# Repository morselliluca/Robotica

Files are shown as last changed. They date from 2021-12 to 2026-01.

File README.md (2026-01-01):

# Robotica

SE NON AVETE VOGLIA DI LEGGERE A FINE README CI SONO LE INFORMAZZIONI PER CONTTATARCI

Tutti i ptogetti robotica del Gruppo DKV Lab<br/>
Siamo un gruppo di 2 persone dell'Itis rossi che hanno partecipato alla Robocup per 4 anni consecutivi con questi progetti.<br/>
il gruppo è formato da:

	Luca Morselli
		-Arduino e Teensyduino:
			-Data collection -> lettura sensori di calore, ultrasuono, riflesso, encoder
			-Serial and comunication -> comunicazione in seriale tra arduino / teensy e Raspberry
			-Movement -> libreria e calibrazione driver e motori dc
		-Pcb design 
		-Mechanical part design
		
	Luca Barban:
		-On Raspberry:
			-Opencv -> riconoscimento caratteri e colori
			-Navigation -> navigazione della mappa
			-Mapping -> creazione della mappa partendo da ultrasuoni o lidar
			-Data Collection -> salvare i dati sulla mappa del nero calore lettere ecc.
			-Serial and comunication -> comunicazione in seriale tra arduino / teensy e Raspberry
			
Cosa troverete all'interno di questa repository:

All'interno di 1. lego line troverete (Line):

	/programmi
		Il codice per la rescue line per un EV3 della lego
		/programmi/Blocchi
			Dei Blocchi custom per leggere il riflesso RGB separatamente da i sensori Stock della lego

All'inerno di 2. project manta troverete (Maze):

	/documentazione
		Un foglio xsl (foglio di calcolo) con tutti i pinout dell'arduino mega, nano e raspberry 
		
	/pcb
		Le Pcb logic e Power usate per il robot + i file gerber per ordinarli
		
	/programma
		/programma/arduino
			/programma/arduino/mega
				il programma per l'arduino mega
			/programma/arduino/nano
				il programma per l'arduino nano
			/programma/arduino/test
				programmi di test vari
		
		/programma/rsby
			programma di test per la raspberry
	
	/scocca
		/scocca/3d
			pezzi da stampare 3d per la scocca (non utilizzati per l'ultima verisone )
		/scocca/logo
			il logo del team
		/scocca/ruote
			ruote da tagliare al laser (non le consiglio, compratele fatte bene Pololu o simili)
		/scocca/taglio
			la scocca del robot da tagliare al laser 
				bello = il piu recente
				manta = delle prove 
				cobra = il primo tentativo
				
	lista.xls 
		la lista dei pezzi che compongono il robot

All'inerno di 3. project Hive troverete (Maze):

	/cagacubi
		le varie versioni del hopper per buttare giu i cubi
		
	/documentazione
		la varia documentazione per tutti i pezzi del robot +  i vari modelli 3d + regole
	
	/foto
		delle foto del robot renderizzato
	
	/pcb 
		file pdf delle schematiche delle 2 pcb del robot + i file gerber per ordinarli
	
	/programma
		/programma/teensy
			il programma per la teensy per interfacciarsi a ros
		/programma/test
			test vari per la teensy e i sensori
	
	/ros documentation
		buona fortuna ragazzi, questo e l'unico pezzo di documentazione ti ros olte il sito ufficiale fatto da cani
	
	/scocca
		disegni di fuzion della scocca del robot per il taglio a laser
	
	/taglio
		progetti in dxf pronti per il taglio laser
		
	Lista.xls
		la lista dei pezzi che compongono il robot

All'inerno di 4. project Help troverete (Line, in aiuto al team A.L.D.O. per i modniali di robotica):

	/La scocca in 3d per la line
	
	/I modelli dai pezzi scelti

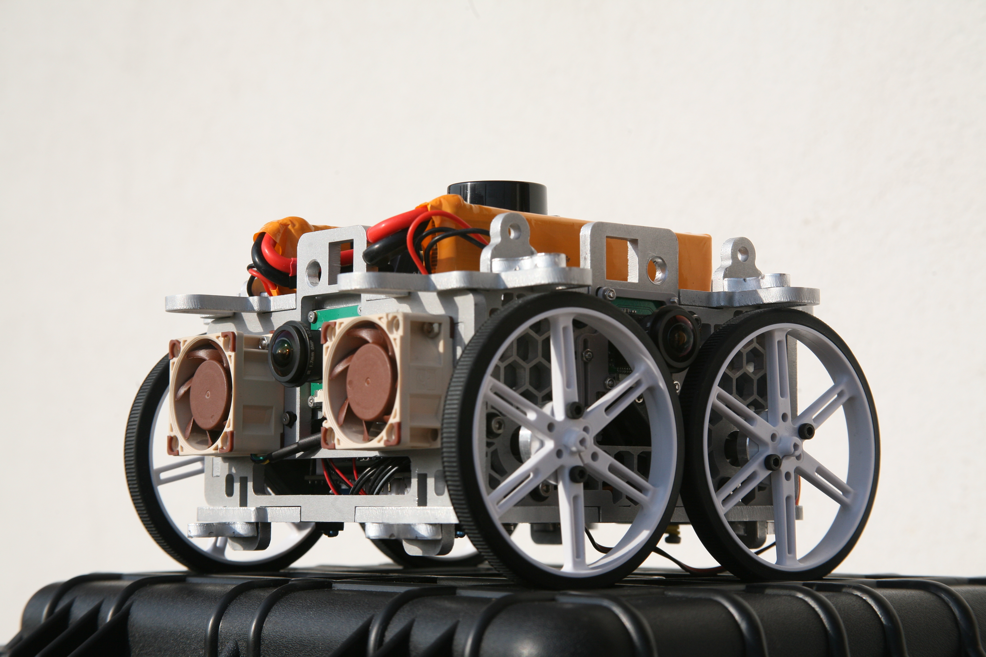
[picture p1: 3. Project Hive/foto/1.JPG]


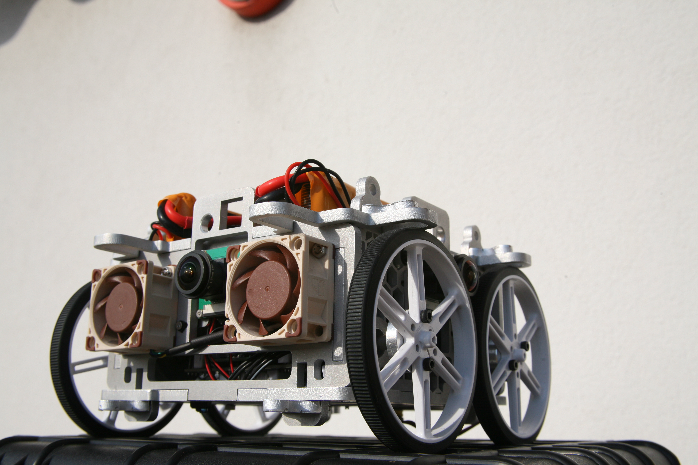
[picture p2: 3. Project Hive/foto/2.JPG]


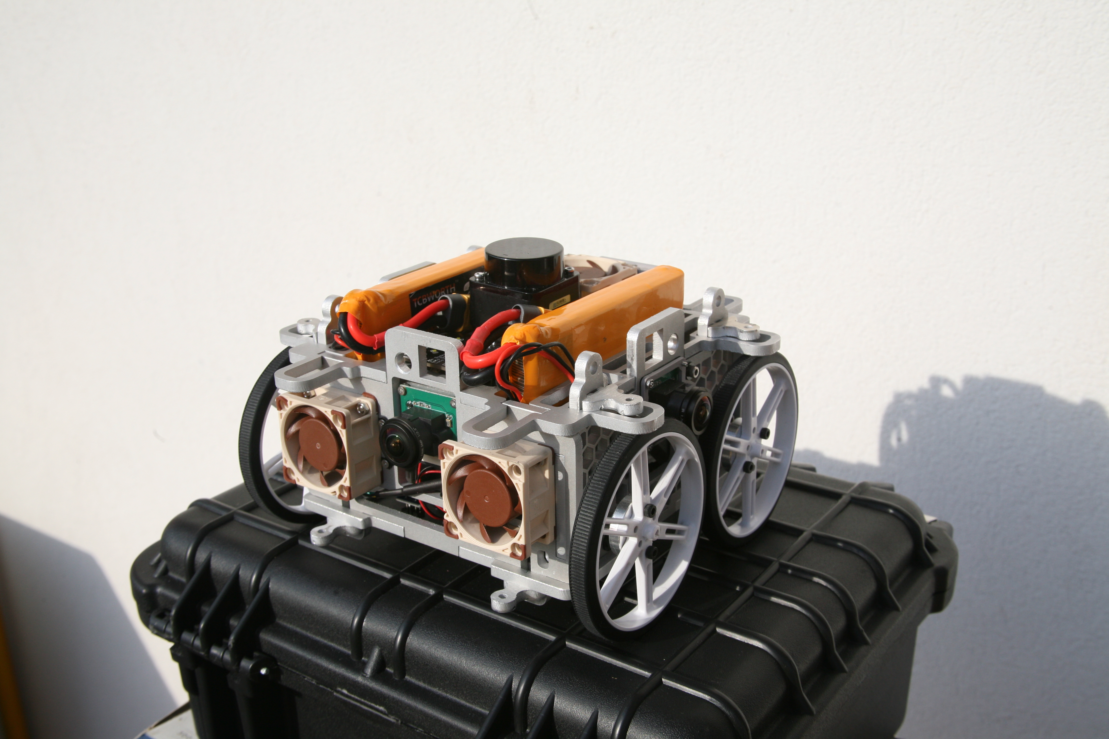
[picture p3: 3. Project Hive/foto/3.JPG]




Faq:

E presente anche una ide di arduino munita di Teensyduino, rosserial e tutte le librerie da noi utilizzate.

Le parti di raspberry degli ultimi 2 progetti mancano e verra aggiunta solo quella dell'ultimo progetto in quanto quella di Manta e stata persa.

I pezzi per il taglio laser sono stati provati principalmente in legno (pippo), plexiglass ed alluminio

I pezzi stampati sono sati stampati solo con stampanti 3d a filamento in quanto della a resina non funzionava (prusa MK.3)

Il grosso dei pezzi e stato acquistato da Aliexpress

Nella lista di Manta ci sono i driver dei motori cinesi NON COMPRATELI si bruciano subito prendete i pololu anche se costano di piu valgono la spesa

Non usate amg8833 come in Manta costano tanto e non e possibile cambiare l'indirizzo i2c nella libreria per leggerli in maniera semplice noi abbiamo usato 2 arduini in piu per questo motvo (i nano), la soluzione migliore e acquistare gli mlx90614

Le batterie consiglio Lipo o 18650 almeno una 3s per portare la tensione intorno i 12v () noi usiamo 2 2s in serie

Consiglio di usare ruote e non cingoli

Consiglio motori con encoder tornano utili per contare i giri che ha fatto la ruota

Per collegare raspberry ad arduino o simili usate la seriale e usate direttamente la porta USB poer evitare di bruciarlo in quanto la maggior parte degli arduino sono a 5v e la raspby supporta solo 3.3v

Quando usate i driver della pololu come MC33926 portate il pin EN -> HIGH e i pin PWM(Negato)/D1 -> Low

I pin INA e INB sono usati per la direzione, vanno messi uno in HIGH uno in LOW 

Da prova_v17 sul progetto Hive le funzioni hanno un timing e vengono eseguite esattamente ogni N millisecondi (la funzione si trova all'interno del void loop)<br/>
	-Odom viene mandata 100HZ<br/>
	-velocita e encoder sono calcolati 1000HZ<br/>

Source:<br/>

Sensori di distanza arduino:<br/>
https://www.youtube.com/watch?v=6F1B_N6LuKw<br/>
https://dronebotworkshop.com/hc-sr04-ultrasonic-distance-sensor-arduino/<br/>

Libreria Pololu vnh5019, la base della libreria custom che troverete in/arduino-1.8.19/libraries/DriverDkv<br/>
https://github.com/pololu/dual-vnh5019-motor-shield<br/>
	
Tutorial per Rosserail + navigation:<br/>
https://www.youtube.com/watch?v=q1u_cC-5Sac<br/>
https://www.youtube.com/watch?v=HLLmV9LQoac<br/>

Ros in generale:<br/>
http://hotblackrobotics.github.io<br/>
https://automaticaddison.com<br/>

Ros navigation:<br/>
https://emanual.robotis.com/docs/en/platform/turtlebot3/learn/#books<br/>
http://wiki.ros.org/ROS/Installation<br/>
http://wiki.ros.org/catkin/Tutorials/create_a_workspace<br/>
http://wiki.ros.org/navigation/Tutorials/RobotSetup<br/>
http://wiki.ros.org/teb_local_planner<br/>
https://answers.ros.org/question/249216/rosserial-posearray-crashes-when-more-than-8-poses-are-used/<br/>

Mlx90614 come usarle e cambiare indirizzo:<br/>
https://www.instructables.com/Multiple-IR-Temperature-Sensors/<br/>
	
Il software per disegnare pcb che consiglio::<br/>
https://easyeda.com/editor<br/>
		
Dove ordinare le pcb online:<br/>
https://jlcpcb.com/<br/>
		
Dove ho ordinato i pezzi tagliati al laser in alluminio:<br/>
https://www.laserboost.com/en/create<br/>
	
Arduino ide (non la 2.0 che non funziona con teensyduino):<br/>
https://www.arduino.cc/en/software<br/>
			
Teensyduino:<br/>
https://www.pjrc.com/teensy/td_usage.html<br/>
https://www.pjrc.com/teensy/teensyduino.html<br/>
https://www.pjrc.com/teensy/td_pulse.html<br/>
https://www.pjrc.com/teensy/td_digital.html<br/>
https://www.pjrc.com/teensy/td_serial.html<br/>
https://www.pjrc.com/teensy/td_uart.html<br/>
		
Software Modellazione 3d (Fusion360 e gratis per gli studenti):<br/>	
https://www.autodesk.com/products/fusion-360/free-trial<br/>

NOTA:<br/>
Usare in maniera informativa nessuno di questi progetti e perfetto ma possono essere usati come una buona base per capire il funzionamento dei vari componenti<br/>
Siamo felici di aiutarvi per qualunque dubbio o perplessita<br/>

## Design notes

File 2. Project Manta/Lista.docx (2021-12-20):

Upgrade

Ci servono

Abbiamo

- 2x amg8833 (telecamere termiche) https://www.melopero.com/shop/sensori/temperatura/melopero-amg8833-grid-eye-ir-array-breakout8833/
- 4x motori(con encoder(non sono uguali a i nostri ma similissimi))

https://www.distrelec.it/it/motore-dc-39-mm-con-cambio-encoder-30-12-vdc-micro-motors-rhe158-30-12v/p/15448402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

- 2x pololu (o simili)

https://www.melopero.com/shop/componenti/pololu-dual-vnh5019-motor-driver-shield-for-arduino/

- 4x telecamere usb

https://www.distrelec.it/it/dash-cam-1280-1024-12-vdc-valueline-svl-carcam10/p/30036026?track=true

- 1x rasperry pi (va bene anche la 3 io ho messo la 4 perche ho trovato questo)

https://www.melopero.com/shop/raspberry-pi-4/raspberry-pi-4-model-b-4gb/

- 1x arduino mega

https://www.melopero.com/shop/arduino-original/arduino-mega-2560-rev3/

- 8x/10x ultrasuoni

https://www.conrad.it/p/sensore-a-ultrasuoni-st1099-iduino-st1099-1616245

- 2x/4x sensori di riflesso
- 2x arduino nano (si puo fare anche senza ma e spararsi nelle palle)

https://www.distrelec.it/it/scheda-nano-arduino-arduino-a000005/p/11096733?track=true

- Legno da 6mm
- 1xRegolatore tesione dc-dc 5v(per raspy)

https://www.melopero.com/shop/componenti/circuiti-integrati/regolatori-circuiti-integrati/pololu-5v-step-upstep-down-voltage-regulator-s7v8f5/

- 1xRegolatore tensione dc-dc 9v(per arduino)

https://www.melopero.com/shop/robotica/pololu-adjustable-step-upstep-down-voltage-regulator-s8v3a/

- 1xRegolatore tensione dc-dc 12v (almeno 4-5A per motori)

https://www.conrad.it/p/scheda-di-sviluppo-buckboost-1875989

- 1xGiroscopio

https://it.rs-online.com/web/p/kit-di-sviluppo-di-sensore/7813033/

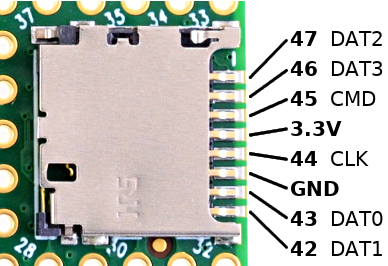
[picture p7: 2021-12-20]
3. Project Hive/Documentazione/Teensy 4.1/Teensy® 4.1_files/teensy41_sdcard_pinout.png

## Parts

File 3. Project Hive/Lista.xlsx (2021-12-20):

Name | Link | Link 3D | -fare o cercare: --oled --batteria -controllare le misure di quelli scaricati -scaricare e uplodare tutti i file sia nella cartella assemblato che nella cartella documentazione (in documentazione ogni pezzo deve avere la sua cartella con il modello 3d e la datasheet se non ce mettilo)
MC33926 | https://www.pololu.com/product/1213
Mlx90614 | https://it.aliexpress.com/item/1005001608889968.html | https://grabcad.com/library/ir-thermo-sensor-hw-691-mlx90614-1
TCRT5000 | https://it.aliexpress.com/item/1899471977.html | https://gallery.autodesk.com/fusion360/projects/135445/sensor-mh-tcrt5000-seguir-trayectoria
LD06 | https://www.inno-maker.com/product/lidar-ld06/
Teensy 4.1 | https://www.sparkfun.com/products/16771
Arducam Multi Camera Adapter Module V2.2 | https://www.uctronics.com/arducam-multi-camera-adapter-module-v2-2-for-raspberry-pi-4-3b-3b-5mp-and-8mp-cameras-compatible-with-arducam-mipi-cameras.html | https://www.uctronics.com/camera-modules/camera-multiplexer/arducam-multi-camera-adapter-module-v2-2-for-raspberry-pi-4-3b-3b-5mp-and-8mp-cameras-compatible-w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
Telecamere | https://it.aliexpress.com/item/1005001597402383.html | https://grabcad.com/library/raspberry-pi-camera-ov5647-1
Ruote | https://www.pololu.com/product/1439 | https://www.pololu.com/product/1439
Adattatori | https://www.pololu.com/product/1083 | https://www.pololu.com/product/1083
Case Rpi | https://it.aliexpress.com/item/1005001691525070.html
Kit jst | https://it.aliexpress.com/item/4000922512405.html
5m cavo awg30 flat 10 fili | https://it.aliexpress.com/item/1841428393.html
Kit jst 8pin | https://it.aliexpress.com/item/1005001628752083.html
ssr | https://it.aliexpress.com/item/32795333121.html
buck converter | https://it.aliexpress.com/item/1005001974967230.html
BNO055 (layout adafruit) | https://it.aliexpress.com/item/1005001641606973.html
condensatore 5v piccolino per raspy | https://it.aliexpress.com/item/32786266119.html
condensatori 12v | https://it.aliexpress.com/item/4000559256747.html
oled arduino i2c quello quadrato non rettangolare | https://it.aliexpress.com/item/1005001908498879.html
Usb c breakout | https://it.aliexpress.com/item/1005001337982060.html
cavi usb micro to usb 90° | https://it.aliexpress.com/item/4000069186507.html
lipo tester | https://it.aliexpress.com/item/4000187507483.html
led Quadrati | https://it.aliexpress.com/item/32954620575.html
Fan 5010 5v | https://it.aliexpress.com/item/32847821588.html | https://gallery.autodesk.com/projects/148644/fan-50x50x10mm?searched=
Raspy | https://www.amazon.com/Raspberry-Model-2019-Quad-Bluetooth/dp/B07TC2BK1X | https://www.thingiverse.com/thing:3778297 |  | Su PCB
Switch | https://www.aliexpress.com/item/32919390284.html | https://gallery.autodesk.com/projects/156746/rocker-toggle-15a-250v-20a-125v-spst-2pin-onoff-switch?searched= |  | Non Servono
Led | https://www.aliexpress.com/item/32874413253.html | https://gallery.autodesk.com/projects/all#query=led&filters=%5B%5D&sort=relevance |  | Fatti da Alin
Batteria |  |  |  | Da Fare
Motore | https://www.banggood.com/Chihai-DC-12V-240rpm-Encoder-Motor-L-Type-Gear-Motor-p-1309847.html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 |  |  | Da Fare

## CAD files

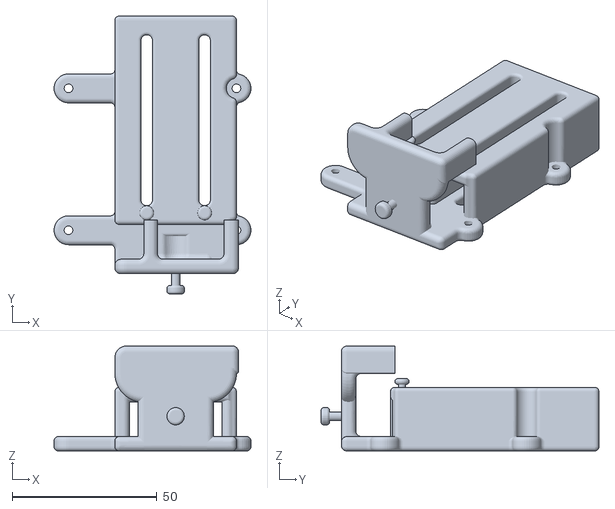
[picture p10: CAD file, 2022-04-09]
3. Project Hive/Mechanics/Cagacubi/Cagacubi v10/Cagacubi v10.stl
68.0 x 96.0 x 36.2

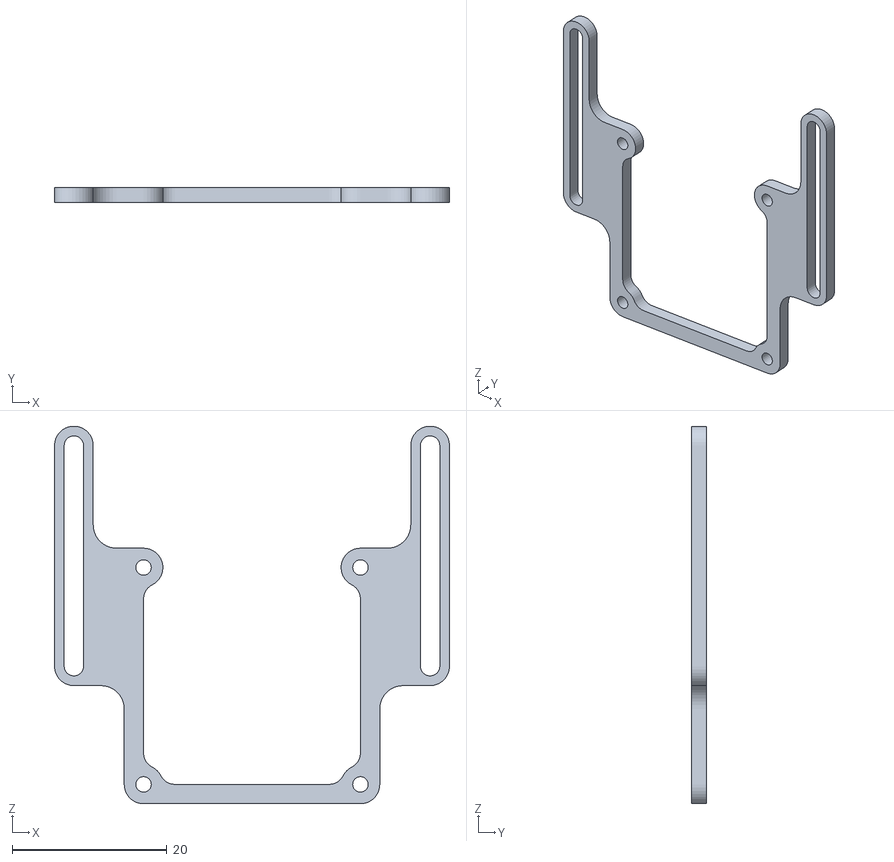
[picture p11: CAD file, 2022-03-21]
3. Project Hive/Mechanics/Cam Holder/Brachet cam v1.stl
51.0 x 2.00 x 48.7

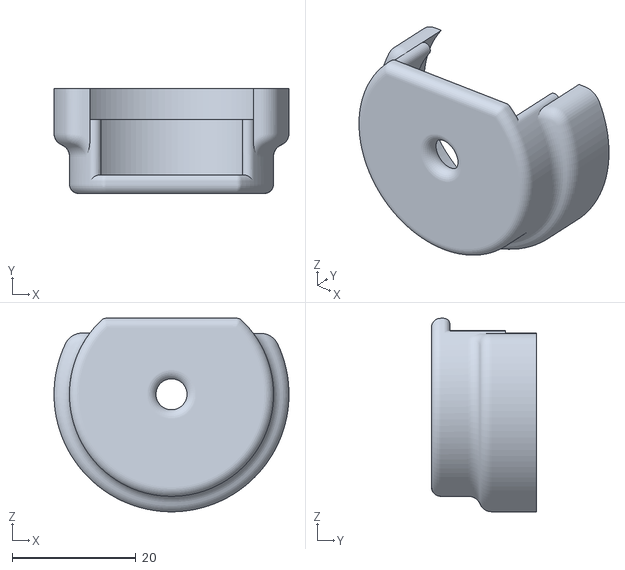
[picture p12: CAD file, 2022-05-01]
3. Project Hive/Mechanics/Motor cover/motor cover v4/motor cover v4.stl
38.0 x 17.0 x 31.3

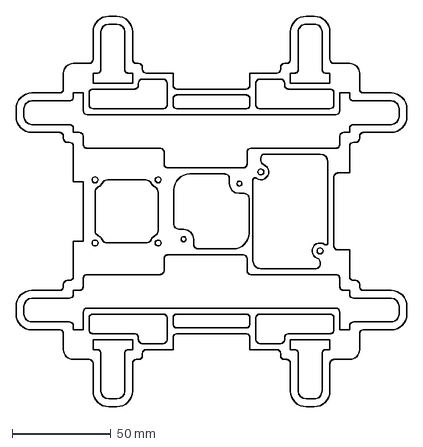
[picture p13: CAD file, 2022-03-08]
3. Project Hive/Mechanics/Scocca/Taglio/Taglio v13/Top.dxf
198.0 x 197.9 mm

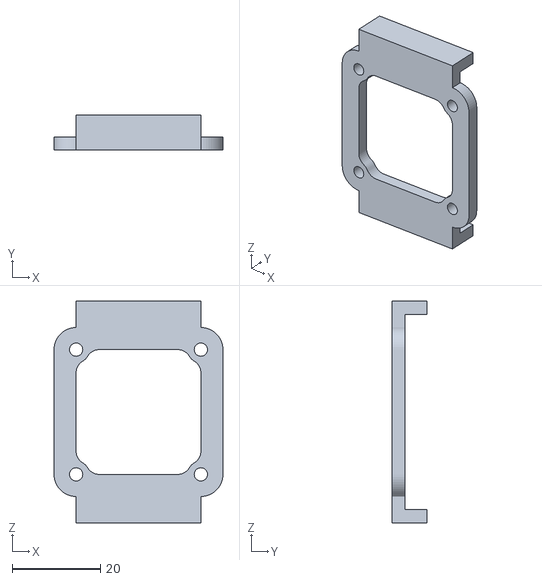
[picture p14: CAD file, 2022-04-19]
3. Project Hive/Mechanics/Spacer/spacer v2.stl
38.2 x 8.00 x 50.2

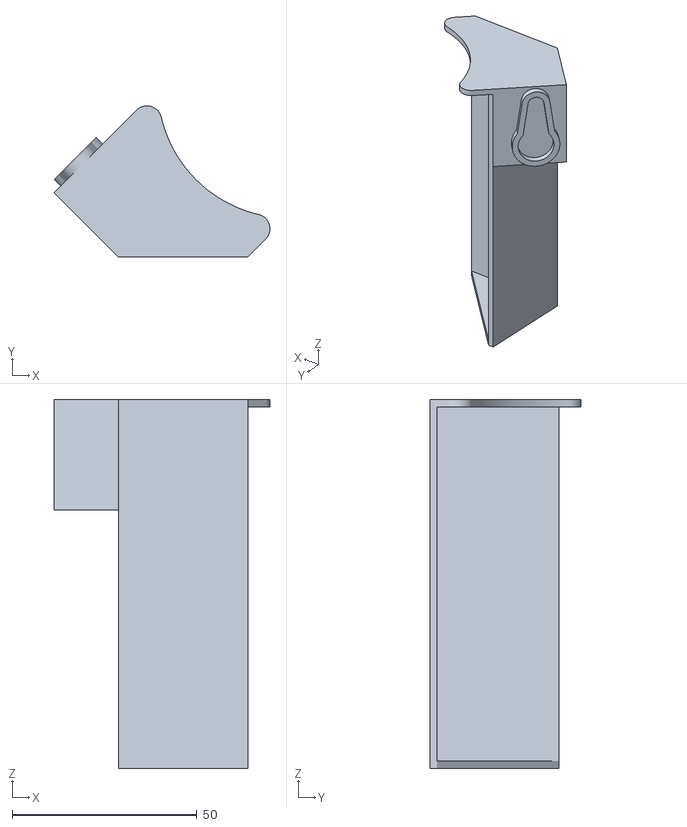
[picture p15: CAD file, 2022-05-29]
4. Project Help/3d print/Scoop R.stl
58.5 x 41.0 x 100.0

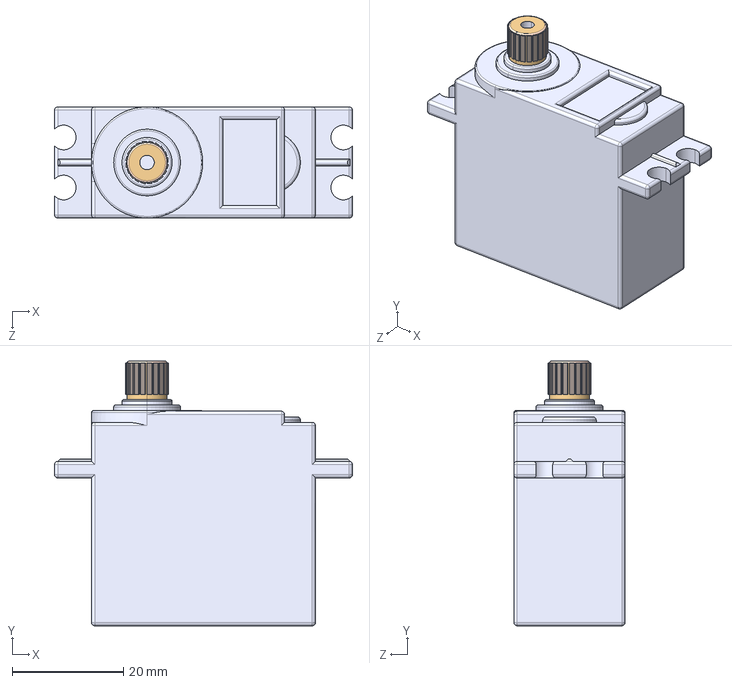
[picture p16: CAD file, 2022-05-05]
4. Project Help/Modelli/Servo MG996R.STEP
53.6 x 47.6 x 20.0 mm

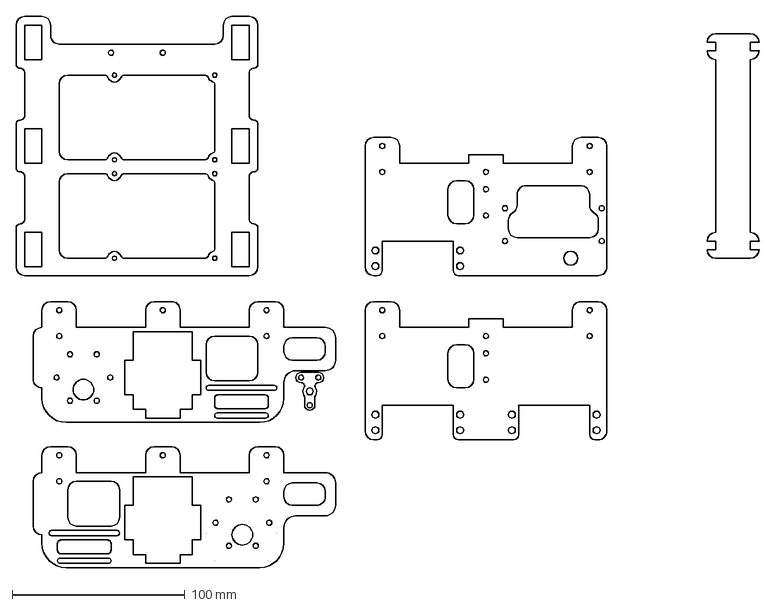
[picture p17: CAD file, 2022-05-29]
4. Project Help/Taglio/taglio.dxf
430.0 x 319.0 mm

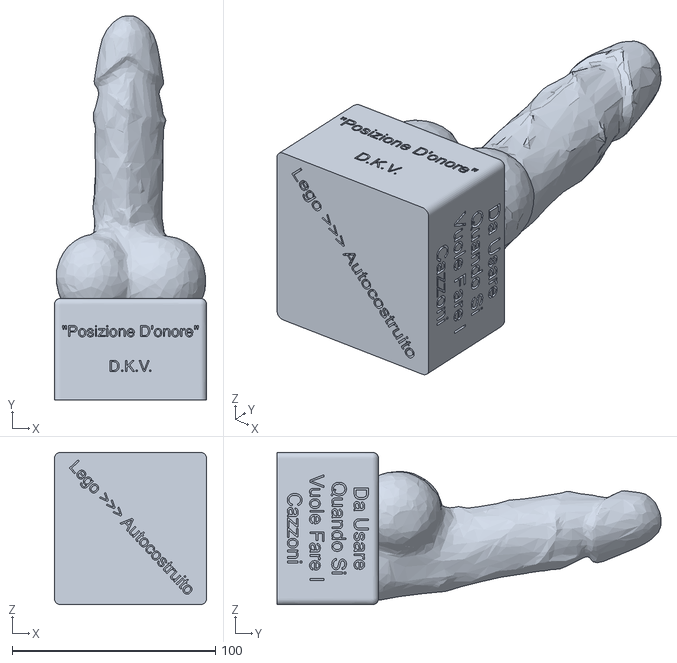
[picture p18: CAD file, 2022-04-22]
Premio/Premio v1.stl
75.0 x 189.1 x 75.0

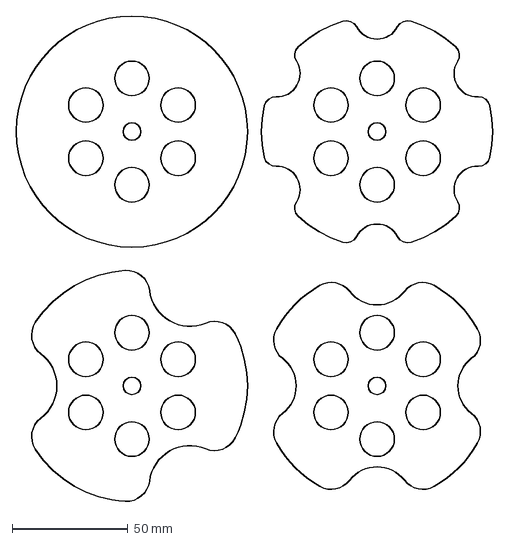
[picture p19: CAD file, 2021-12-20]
2. Project Manta/scocca/ruote/ruote1.DXF
206.4 x 210.2 mm

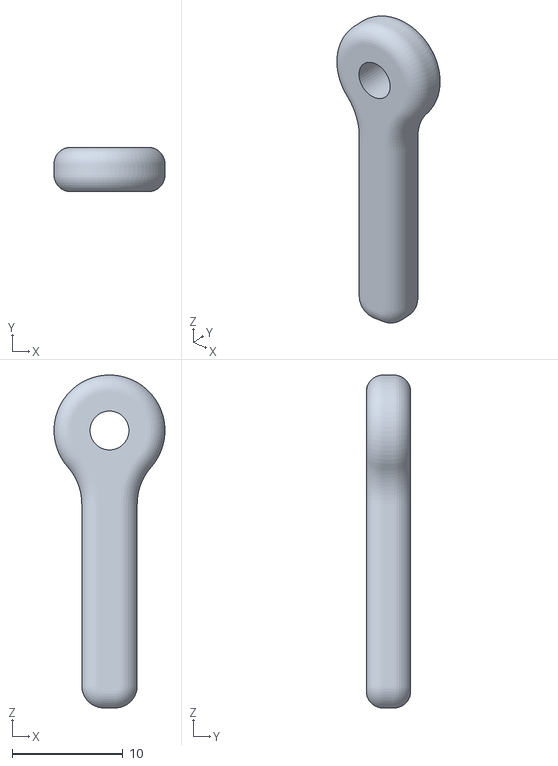
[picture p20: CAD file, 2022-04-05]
3. Project Hive/Mechanics/Cagacubi/Cagacubi v10/lever v10.stl
10.00 x 4.00 x 30.0

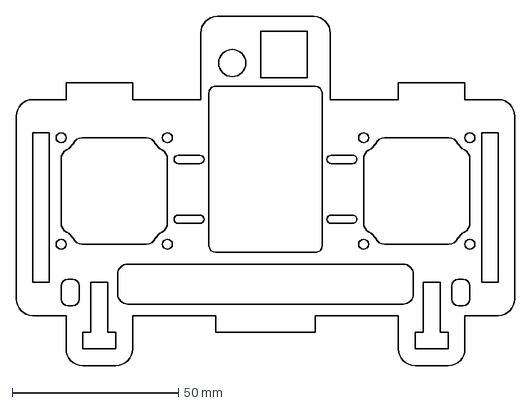
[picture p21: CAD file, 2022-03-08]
3. Project Hive/Mechanics/Scocca/Taglio/Taglio v13/Front.dxf
150.0 x 105.0 mm

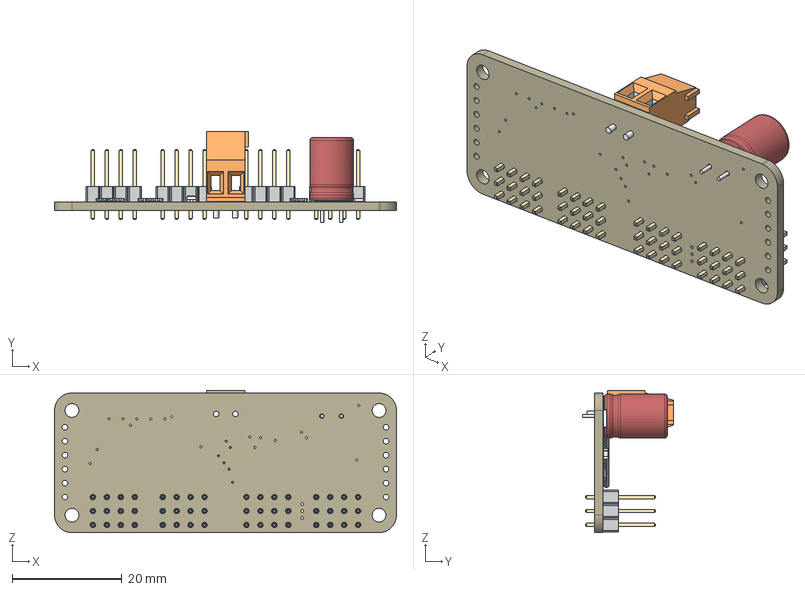
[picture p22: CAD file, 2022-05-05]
4. Project Help/Modelli/PCA9685.step
62.2 x 16.6 x 25.9 mm
Board
Pins x 12
Case x 12
tssop_28
terminal_weidmuller_2way_1667750000
CAP_8X11.5_P3
CAT16-J4 x 6
LTST-C150KGKT_Base
LTST-C150KGKT_AnodeMark
LTST-C150KGKT_AnodeTerminal
LTST-C150KGKT_CathodeTerminal
LTST-C150KGKT_CathodeMark
LTST-C150KGKT_LedDice
LTST-C150KGKT_Lens
LTST-C150KGKT_GreenMark x 2
Pin1Body x 2
Pin2Body x 2
CeramicBody x 2
CoatingBody x 2
Case_1
Contacts

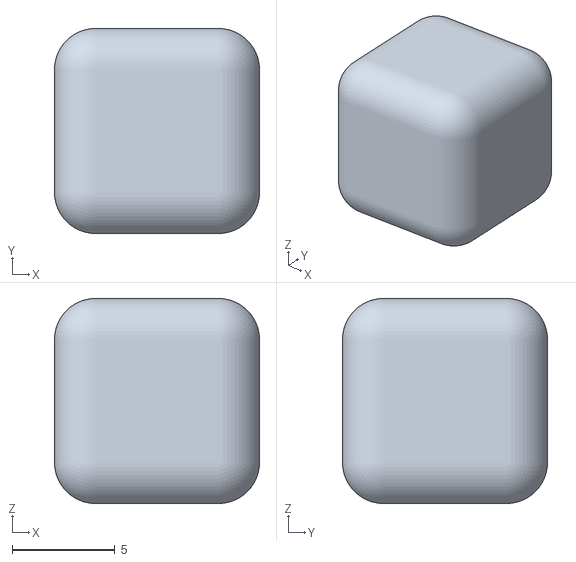
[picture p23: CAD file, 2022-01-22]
3. Project Hive/Mechanics/Cagacubi/Cagacubi v10/cubo v10.stl
10.0 x 10.0 x 10.0

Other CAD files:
4. Project Help/3d print/Scoop L.stl
3. Project Hive/Mechanics/Scocca/Taglio/Taglio v13/Back.dxf
4. Project Help/3d print/spacer x6.stl
4. Project Help/Modelli/VL6180X-Time_of_Flight_Sensor.stp
2. Project Manta/scocca/3d/inutili/L/L_1.0.f3d
2. Project Manta/scocca/3d/inutili/L/L_1.1.f3d
2. Project Manta/scocca/3d/inutili/angoli/angoli_1.0.f3d
2. Project Manta/scocca/3d/inutili/angoli/angoli_1.1.f3d
2. Project Manta/scocca/3d/inutili/ruote/ruote_1.0 v1.f3d
2. Project Manta/scocca/3d/inutili/ruote/ruote_1.0 v2.f3d
2. Project Manta/scocca/3d/inutili/ruote/ruote_1.0 v3.f3d
2. Project Manta/scocca/3d/inutili/ruote/ruote_1.0 v4.f3d
2. Project Manta/scocca/3d/inutili/ruote/ruote_1.0 v5.f3d
2. Project Manta/scocca/3d/inutili/ruote/ruote_1.0 v6.f3d
2. Project Manta/scocca/3d/inutili/ruote/ruote_1.0 v7.f3d
2. Project Manta/scocca/3d/inutili/ruote/ruote_1.0 v8.f3d
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

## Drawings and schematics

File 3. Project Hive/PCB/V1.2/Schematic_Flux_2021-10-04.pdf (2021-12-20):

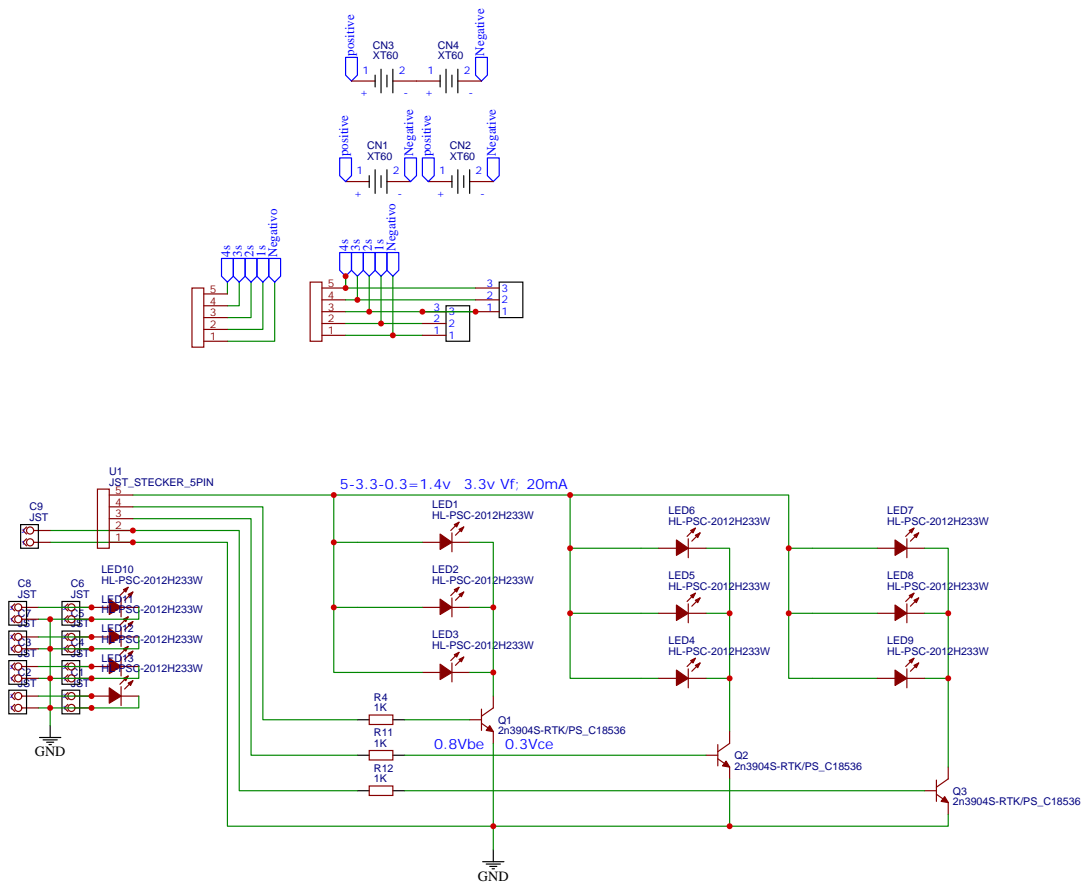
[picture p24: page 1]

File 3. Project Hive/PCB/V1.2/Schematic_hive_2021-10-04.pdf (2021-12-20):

IR

## LM2596 MINI MODULE

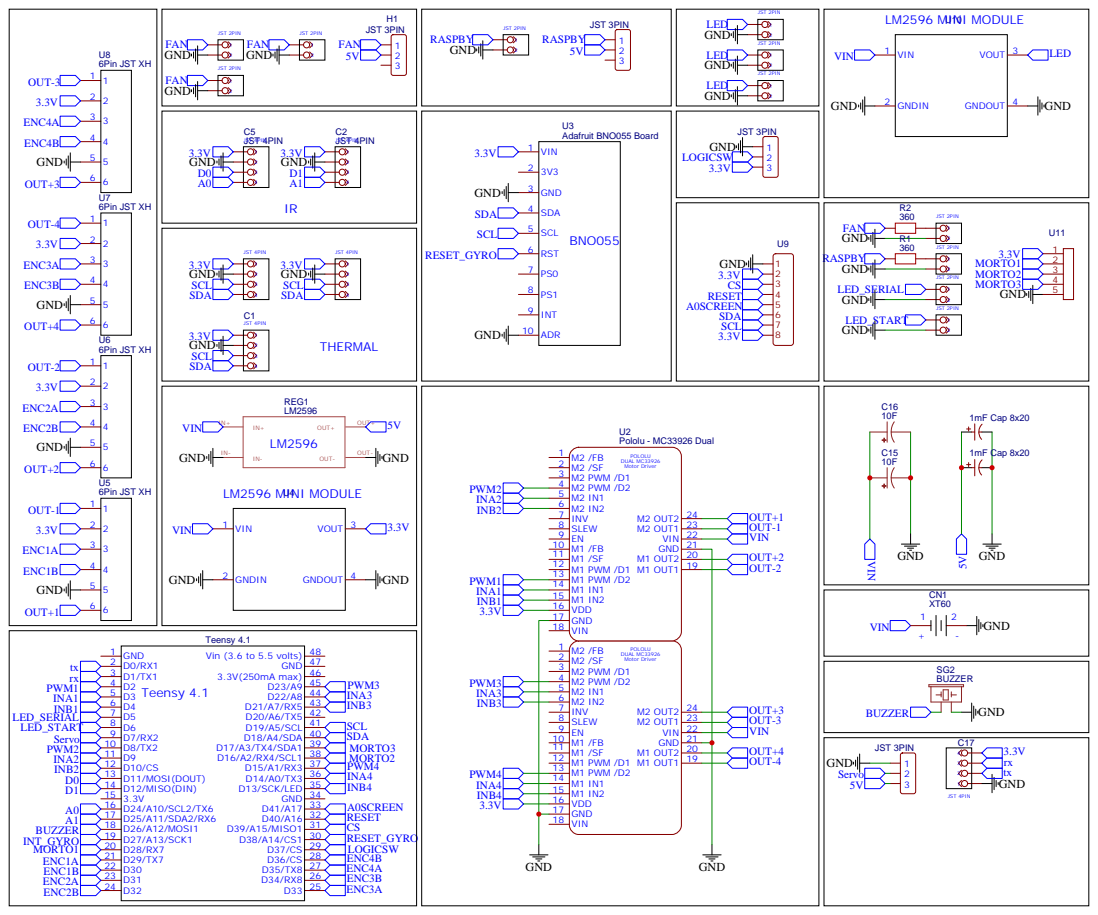
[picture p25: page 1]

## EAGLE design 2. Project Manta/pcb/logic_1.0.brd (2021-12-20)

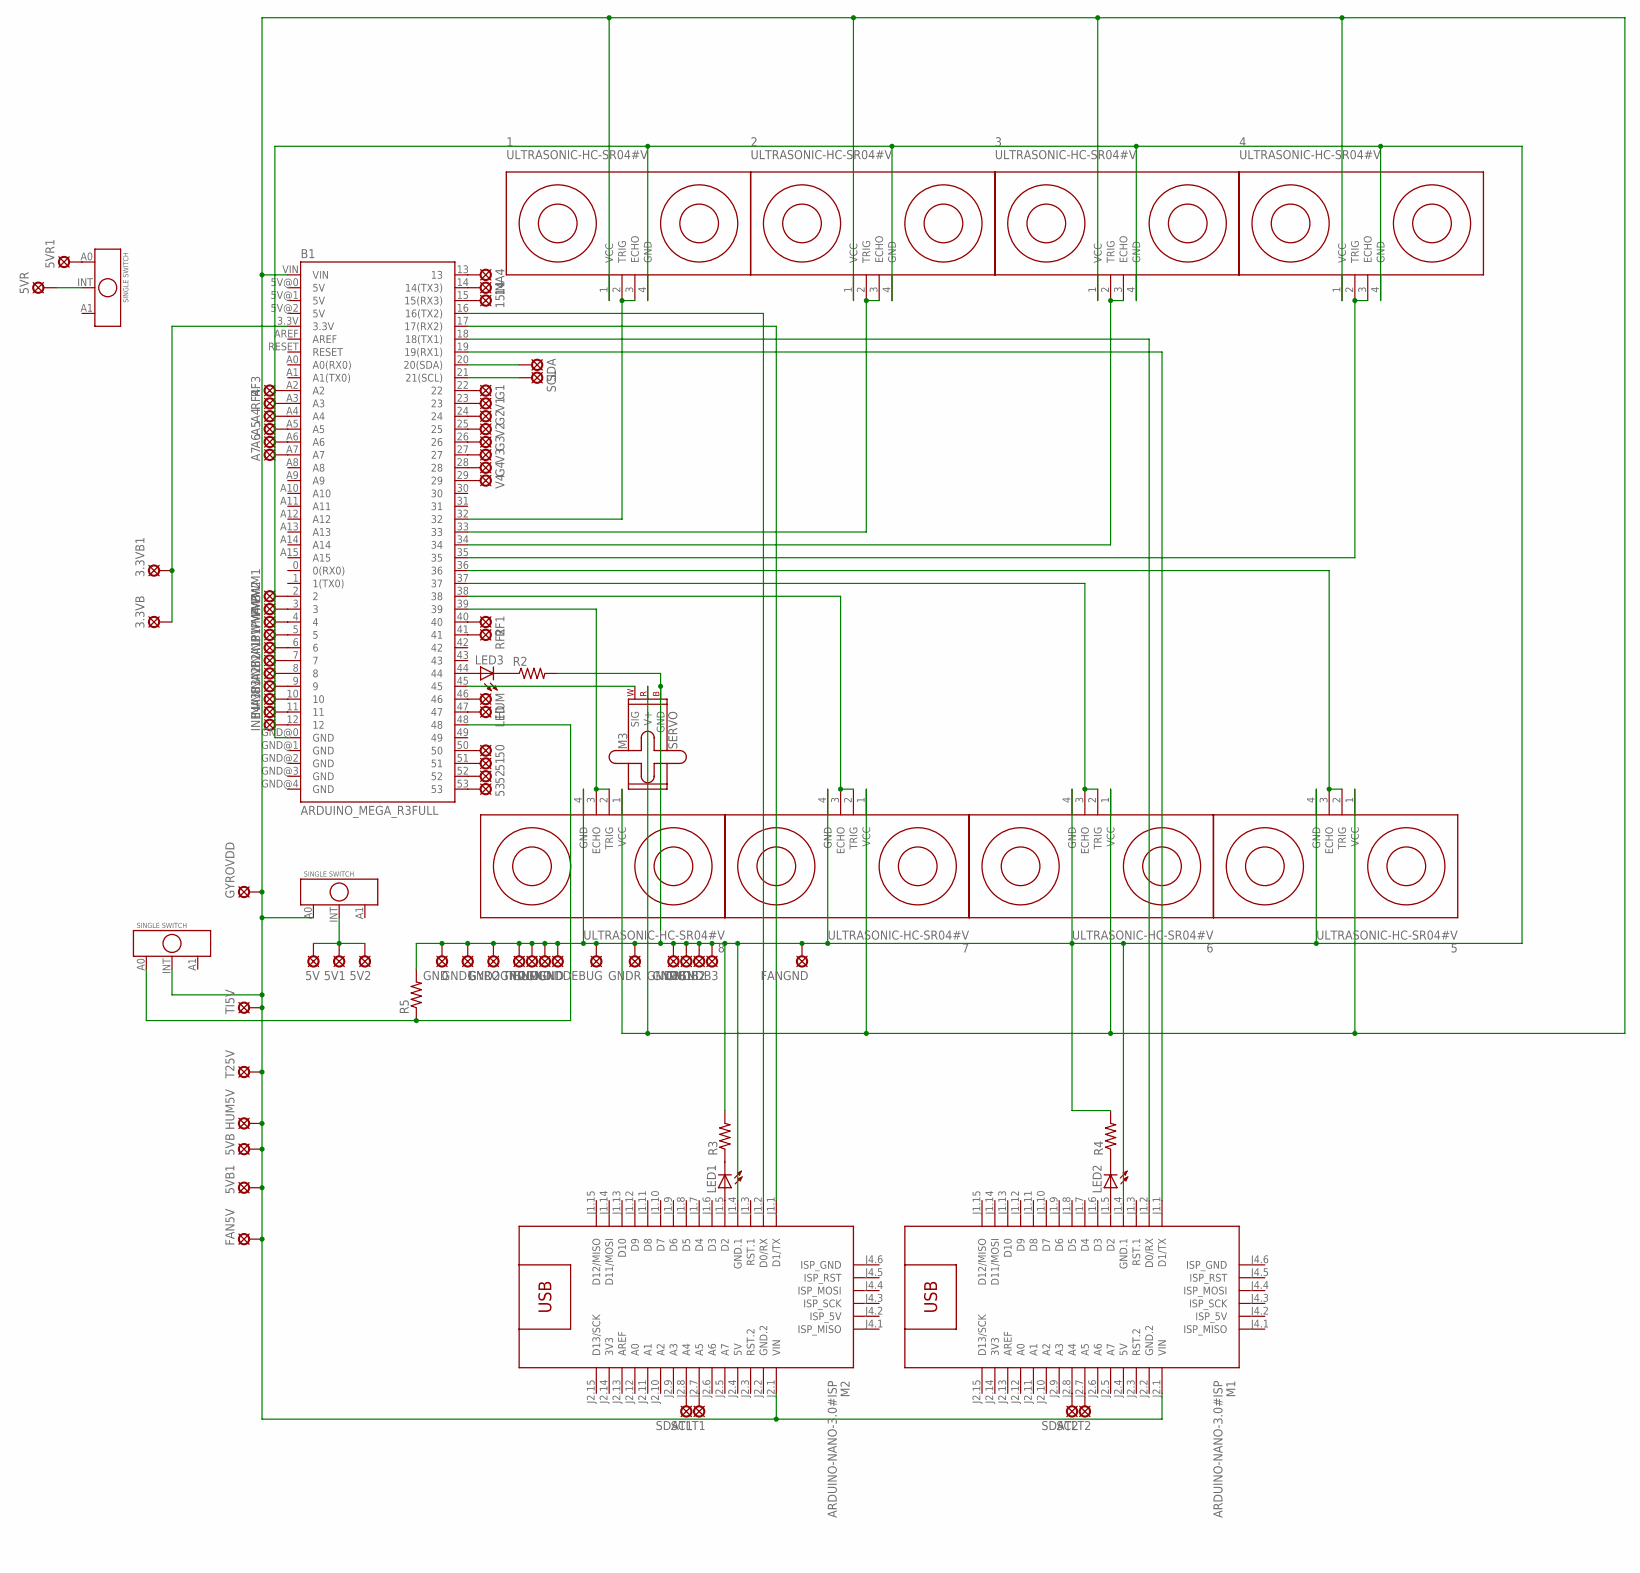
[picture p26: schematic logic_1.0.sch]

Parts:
1, 2, 3, 4, 5, 6, 7, 8: ULTRASONIC-HC-SR04#V
3.3VB, 3.3VB1, 5V, 5V1, 5V2, 5VB, 5VB1, 5VR, 5VR1, 14, 15, 50, 51, 52, 53: LSP10
A4, A5, A6, A7: LSP10
B1: ARDUINO_MEGA_R3FULL; ARDUINO_MEGA
FAN5V: LSP10
FANGND: LSP10
G1, G2, G3, G4: LSP10
GND, GND1, GND2: LSP10
GNDB, GNDB1, GNDB2, GNDB3: LSP10
GNDDEBUG: LSP10
GNDR: LSP10
GYROGND: LSP10
GYROVDD: LSP10
HUM, HUM5V: LSP10
HUMGND: LSP10
INA1, INA2, INA3, INA4: LSP10
INB1, INB2, INB3, INB4: LSP10
LED: LSP10
LED1, LED2, LED3: LED5MM
M1, M2: ARDUINO-NANO-3.0#ISP
M3: SERVO; 1X03
PWM1, PWM2, PWM3, PWM4: LSP10
R2, R3, R4, R5: R-US_0207/10; 0207/10
RF1, RF2, RF3, RF4: LSP10
SCL: LSP10
SCLT1, SCLT2: LSP10
SDA: LSP10
SDAT1, SDAT2: LSP10
T2GND, T25V: LSP10
TI5V: LSP10
TIGND: LSP10
U$1, U$2, U$3: SINGE_SWITCH; SINGLE_SWITCH
V1, V2, V3, V4: LSP10

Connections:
3V3: M1.J2.14 (3V3), M2.J2.14 (3V3)
5V: M1.J2.4 (5V), M2.J2.4 (5V)
GND: 1.4 (GND), 2.4 (GND), 3.4 (GND), 4.4 (GND), 5.4 (GND), 6.4 (GND), 7.4 (GND), 8.4 (GND), B1.GND@0 (GND), FANGND.MP, GND.MP, GND1.MP, GND2.MP, GNDB.MP, GNDB1.MP, GNDB2.MP, GNDB3.MP, GNDDEBUG.MP, GNDR.MP, GYROGND.MP, HUMGND.MP, M1.J1.4 (GND.1), M2.J1.4 (GND.1), M3.3 (GND), R2.2, R3.2, R4.2, R5.2, T2GND.MP, TIGND.MP
GND.2: M1.J2.2 (GND.2), M2.J2.2 (GND.2)
unnamed: 5VR1.MP, U$2.A0
unnamed: 5V.MP, 5V1.MP, 5V2.MP, U$1.INT
unnamed: B1.2, PWM1.MP
unnamed: B1.16 (16(TX2)), M2.J1.2 (D0/RX)
unnamed: B1.17 (17(RX2)), M2.J1.1 (D1/TX)
unnamed: B1.18 (18(TX1)), M1.J1.2 (D0/RX)
unnamed: B1.19 (19(RX1)), M1.J1.1 (D1/TX)
unnamed: 1.2 (TRIG), 1.3 (ECHO), B1.32
unnamed: 2.2 (TRIG), 2.3 (ECHO), B1.33
unnamed: 3.2 (TRIG), 3.3 (ECHO), B1.34
unnamed: 4.2 (TRIG), 4.3 (ECHO), B1.35
unnamed: 5.2 (TRIG), 5.3 (ECHO), B1.36
unnamed: 6.2 (TRIG), 6.3 (ECHO), B1.37
unnamed: 7.2 (TRIG), 7.3 (ECHO), B1.38
unnamed: 8.2 (TRIG), 8.3 (ECHO), B1.39
unnamed: B1.45, M3.1 (SIG)
unnamed: 1.1 (VCC), 2.1 (VCC), 3.1 (VCC), 4.1 (VCC), 5.1 (VCC), 5VB.MP, 5VB1.MP, 6.1 (VCC), 7.1 (VCC), 8.1 (VCC), B1.VIN, FAN5V.MP, GYROVDD.MP, HUM5V.MP, M1.J2.1 (VIN), M2.J2.1 (VIN), M3.2 (V+), T25V.MP, TI5V.MP, U$1.A0, U$3.INT
unnamed: B1.3, PWM2.MP
unnamed: B1.4, PWM3.MP
unnamed: B1.5, PWM4.MP
unnamed: B1.6, INB1.MP
unnamed: B1.7, INA1.MP
unnamed: B1.8, INB2.MP
unnamed: B1.9, INA2.MP
unnamed: B1.10, INB3.MP
unnamed: B1.11, INA3.MP
unnamed: B1.12, INB4.MP
unnamed: B1.13, INA4.MP
unnamed: B1.22, G1.MP
unnamed: B1.23, V1.MP
unnamed: B1.24, G2.MP
unnamed: B1.25, V2.MP
unnamed: B1.26, G3.MP
unnamed: B1.27, V3.MP
unnamed: B1.28, G4.MP
unnamed: B1.29, V4.MP
unnamed: B1.20 (20(SDA)), SDA.MP
unnamed: B1.21 (21(SCL)), SCL.MP
unnamed: B1.46, HUM.MP
unnamed: B1.47, LED.MP
unnamed: 3.3VB.MP, 3.3VB1.MP, B1.3.3V
unnamed: M2.J2.8 (A4), SDAT1.MP
unnamed: M2.J2.7 (A5), SCLT1.MP
unnamed: M1.J2.8 (A4), SDAT2.MP
unnamed: M1.J2.7 (A5), SCLT2.MP
unnamed: B1.40, RF1.MP
unnamed: B1.44, LED3.A
unnamed: B1.41, RF2.MP
unnamed: 5VR.MP, U$2.INT
unnamed: B1.A2, RF3.MP
unnamed: B1.A3, RF4.MP
unnamed: LED1.A, M2.J1.5 (D2)
unnamed: LED2.A, M1.J1.5 (D2)
unnamed: LED3.K (C), R2.1
unnamed: LED2.K (C), R4.1
unnamed: LED1.K (C), R3.1
unnamed: 50.MP, B1.50
unnamed: 51.MP, B1.51
unnamed: 52.MP, B1.52
unnamed: A6.MP, B1.A6
unnamed: A7.MP, B1.A7
unnamed: A4.MP, B1.A4
unnamed: A5.MP, B1.A5
unnamed: 53.MP, B1.53
unnamed: B1.48, R5.1, U$3.A0
unnamed: 14.MP, B1.14 (14(TX3))
unnamed: 15.MP, B1.15 (15(RX3))

Board: 2 copper layers, 92 parts (1 on the bottom side), 71 nets, no tracks yet.

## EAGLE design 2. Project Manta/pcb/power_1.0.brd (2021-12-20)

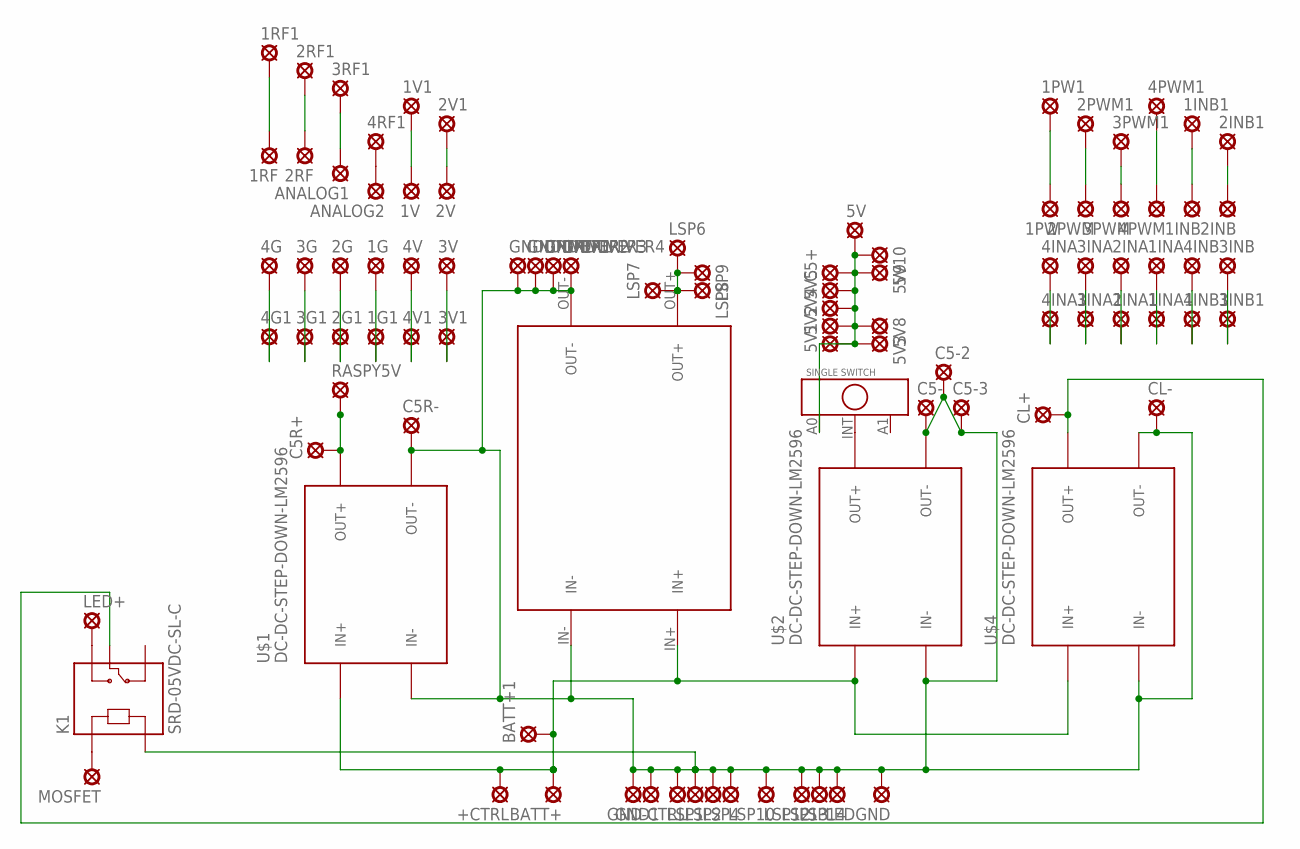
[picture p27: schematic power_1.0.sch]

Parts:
1G, 1G1, 1INA, 1INA1, 1INB, 1INB1, 1PW, 1PW1, 1RF, 1RF1, 1V, 1V1, 2G, 2G1, 2INA, 2INA1, 2INB, 2INB1, 2PWM, 2PWM1, 2RF, 2RF1, 2V, 2V1, 3G, 3G1, 3INA, 3INA1, 3INB, 3INB1, 3PWM, 3PWM1, 3RF1, 3V, 3V1, 4G, 4G1, 4INA, 4INA1, 4INB, 4INB1, 4PWM, 4PWM1, 4RF1, 4V, 4V1, 5V, 5V1, 5V2, 5V3, 5V4, 5V5, 5V8, 5V9, 5V10: LSP10
+CTRL: LSP10
-CTRL: LSP10
ANALOG1, ANALOG2: LSP10
BATT+, BATT+1: SE14
C5+, C5-, C5-2, C5-3, C5R+, C5R-: LSP10
CL+: LSP10
CL-: LSP10
GND, GND1: SE14
GNDDRIVER1, GNDDRIVER2, GNDDRIVER3, GNDDRIVER4: SE14
K1: SRD-05VDC-SL-C; RELAY_SRD-05VDC-SL-C
LED+: SE14
LEDGND: SE14
LSP1, LSP2, LSP4, LSP10, LSP12, LSP13, LSP14: LSP10
LSP6, LSP7, LSP8, LSP9: SE14
MOSFET: LSP10
RASPY5V: LSP10
U$1, U$2, U$4: DC-DC-STEP-DOWN-LM2596
U$3: DC-DCSTEPUP/DOWNBUCKCONVERTER
U$5: SINGE_SWITCH; SINGLE_SWITCH

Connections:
GND: -CTRL.MP, C5-.MP, C5-2.MP, C5-3.MP, C5R-.MP, CL-.MP, GND.MP, GND1.MP, GNDDRIVER1.MP, GNDDRIVER2.MP, GNDDRIVER3.MP, GNDDRIVER4.MP, K1.A2, LEDGND.MP, LSP1.MP, LSP2.MP, LSP4.MP, LSP10.MP, LSP12.MP, LSP13.MP, LSP14.MP, U$1.IN-, U$1.OUT-, U$2.IN-, U$2.OUT-, U$3.IN-, U$3.OUT-, U$4.IN-, U$4.OUT-
unnamed: U$2.OUT+, U$5.INT
unnamed: LSP6.MP, LSP7.MP, LSP8.MP, LSP9.MP, U$3.OUT+
unnamed: C5R+.MP, RASPY5V.MP, U$1.OUT+
unnamed: 5V.MP, 5V1.MP, 5V2.MP, 5V3.MP, 5V4.MP, 5V5.MP, 5V8.MP, 5V9.MP, 5V10.MP, C5+.MP, U$5.A0
unnamed: 4G.MP, 4G1.MP
unnamed: 3G.MP, 3G1.MP
unnamed: 2G.MP, 2G1.MP
unnamed: 1G.MP, 1G1.MP
unnamed: 4V.MP, 4V1.MP
unnamed: 3V.MP, 3V1.MP
unnamed: 2V.MP, 2V1.MP
unnamed: 1V.MP, 1V1.MP
unnamed: 4RF1.MP, ANALOG2.MP
unnamed: 3RF1.MP, ANALOG1.MP
unnamed: 2RF.MP, 2RF1.MP
unnamed: 1RF.MP, 1RF1.MP
unnamed: 1PW.MP, 1PW1.MP
unnamed: 2PWM.MP, 2PWM1.MP
unnamed: 4INA.MP, 4INA1.MP
unnamed: 3INA.MP, 3INA1.MP
unnamed: 2INA.MP, 2INA1.MP
unnamed: 1INA.MP, 1INA1.MP
unnamed: 4INB.MP, 4INB1.MP
unnamed: 3INB.MP, 3INB1.MP
unnamed: 3PWM.MP, 3PWM1.MP
unnamed: 4PWM.MP, 4PWM1.MP
unnamed: 1INB.MP, 1INB1.MP
unnamed: 2INB.MP, 2INB1.MP
unnamed: K1.NO, LED+.MP
unnamed: K1.A1, MOSFET.MP
unnamed: CL+.MP, K1.COM, U$4.OUT+
unnamed: +CTRL.MP, BATT+.MP, BATT+1.MP, U$1.IN+, U$2.IN+, U$3.IN+, U$4.IN+

Board: 2 copper layers, 96 parts (0 on the bottom side), 33 nets, no tracks yet.

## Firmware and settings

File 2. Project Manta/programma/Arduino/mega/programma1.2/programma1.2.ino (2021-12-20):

#include <SoftwareSerial.h>
#include <Wire.h>
#include <SPI.h>

#define ma1 6
#define mb1 7
#define pwm1 2

#define ma2 8
#define mb2 9
#define pwm2 3

#define ma3 11
#define mb3 10
#define pwm3 4

#define ma4 13
#define mb4 12
#define pwm4 5

#define velocita 125

bool msg = true;
byte input = "";





 #define outputA1 22
 #define outputB1 23

 #define outputA2 24
 #define outputB2 25

 #define outputA3 26
 #define outputB3 27

 #define outputA4 28
 #define outputB4 29
 
 int counter1 = 0; 
 int aState1;
 int aLastState1;  

 int counter2 = 0; 
 int aState2;
 int aLastState2; 

 int counter3 = 0; 
 int aState3;
 int aLastState3; 

 int counter4 = 0; 
 int aState4;
 int aLastState4; 

 int media;
 bool controllo;




const int pingPin = 32;
const int pingPin1 = 33;
const int pingPin2 = 34;
const int pingPin3 = 35;
const int pingPin4 = 36;
const int pingPin5 = 37;
const int pingPin6 = 38;
const int pingPin7 = 39;
const int buttonPin = 50;
char raspy[3][3];
int pingArray[4][2] = { {pingPin, pingPin7},   //davanti
                        {pingPin1, pingPin2},  //sinistra
                        {pingPin3, pingPin4}, //dietro
                        {pingPin5, pingPin6}  //destra
                      }; 
long duration, cm;
float medie[4][2]; 
float somma;
int errore;
char mystr[2];


 int vel1 = 90; 
 int vel2 = 90;
 int vel3 = 90;
 int vel4 = 90; 







#define MPU 0x68
double AcX,AcY,AcZ;
int angolo, angoloiniziale;



//SoftwareSerial mySerial1(16, 17); // RX, TX
//SoftwareSerial mySerial2(18, 19); // RX, TX



void setup()
{
init_MPU();

  
pinMode(pwm1,OUTPUT) ;   //we have to set PWM pin as output
pinMode(ma1,OUTPUT) ;  //Logic pins are also set as output
pinMode(mb1,OUTPUT) ;

pinMode(pwm2,OUTPUT) ;   //we have to set PWM pin as output
pinMode(ma2,OUTPUT) ;  //Logic pins are also set as output
pinMode(mb2,OUTPUT) ;

pinMode(pwm3,OUTPUT) ;   //we have to set PWM pin as output
pinMode(ma3,OUTPUT) ;  //Logic pins are also set as output
pinMode(mb3,OUTPUT) ;

pinMode(pwm4,OUTPUT) ;   //we have to set PWM pin as output
pinMode(ma4,OUTPUT) ;  //Logic pins are also set as output
pinMode(mb4,OUTPUT) ;

   pinMode (outputA1,INPUT);
   pinMode (outputB1,INPUT);
   pinMode (outputA2,INPUT);
   pinMode (outputB2,INPUT);
   pinMode (outputA3,INPUT);
   pinMode (outputB3,INPUT);
   pinMode (outputA4,INPUT);
   pinMode (outputB4,INPUT);
   
   Serial.begin (9600);
   
   aLastState1 = digitalRead(outputA1);   
   aLastState2 = digitalRead(outputA2);
   aLastState3 = digitalRead(outputA3);
   aLastState4 = digitalRead(outputA4);
}

void loop()
{

  //Serial1.readBytes(mystr,1);
  //Serial1.println(mystr); 

  //Serial2.readBytes(mystr,1);
  //Serial2.println(mystr); 
  
  if (Serial.available()>0 && msg){
  Serial.println("----- Test movimento motori -----");
  Serial.println("   Utilizzare WASD per muoversi  ");
  Serial.println("  Utilizzare Q ed E per ruotare  ");
  Serial.println(" Utilizzare P per usare i sensori");
  Serial.println("---------------------------------");
  msg = false;
  }
  if (Serial.available()>0){
    input = Serial.read();
    if (input == 'w') {avanti(255);}
     else if (input == 'a'){ sinistra(255);}
     else if (input == 's'){ indietro(255);}
     else if (input == 'd'){ destra(255);}
     else if (input == 'q'){ girasinistra(255);}
     else if (input == 'e'){ giradestra(255);}
     else if (input == 'p'){ sensori();}
  }
}







///////////////////////////////motori/////////////////////////////////

void avanti (int vel) { //direzioni dei motori messe a caso 😂/
  //motors(vel,vel,vel,vel,1,1,1,1);
  movimento('w');
}
void indietro (int vel) {
  //motors(vel,vel,vel,vel,2,2,2,2);
  movimento('s');
}
void destra (int vel) {
  //motors(vel,vel,vel,vel,1,2,1,2);
  movimento('d');
}
void sinistra (int vel) {
  //motors(vel,vel,vel,vel,2,1,2,1);
  movimento('a');
}
void giradestra (int vel) {
  angoloiniziale=FunctionsPitchRoll(AcY, AcX, AcZ);
  //motors(vel,vel,vel,vel,1,1,2,2);
  movimento('e');
}
void girasinistra (int vel) {
  angoloiniziale=FunctionsPitchRoll(AcY, AcX, AcZ);
  //motors(vel,vel,vel,vel,2,2,1,1);
  movimento('q');
}
void ferma () {
  //motors(0,0,0,0,0,0,0,0);
  alt();
}



////////////////////////movimento/////////////////////

void movimento (char direzione){

   if(direzione=='w'){

    do{
    media=encoder();
    fwd(vel1, vel2, vel3, vel4);
    }while(media<200);
    alt();
    //////////////avanti////////////
    }else if(direzione=='s'){
      
    do{
    media=encoder();
    bk(vel1, vel2, vel3, vel4);
    }while(media<200);
    alt();
    //////////////indietro////////////
    }else if(direzione=='q'){
      
    do{
    FunctionsMPU();
    gsx(vel1, vel2, vel3, vel4);
    angolo=angoloiniziale-FunctionsPitchRoll(AcX, AcY, AcZ);
    }while(abs(angolo)<90);
    alt();
    //////////////gsinistra////////////
    }else if(direzione=='e'){
      
    do{
    gdx(vel1, vel2, vel3, vel4);
    angolo=angoloiniziale-FunctionsPitchRoll(AcX, AcY, AcZ);
    }while(abs(angolo)<90);
    alt( );
    //////////////gdestra////////////
    }else if(direzione=='a'){
      
    do{

    sx(vel1, vel2, vel3, vel4);
    }while(media<200);
    alt();
    //////////////sinistra////////////
    }else if(direzione=='d'){
      
    do{

    dx(vel1, vel2, vel3, vel4);
    }while(media<200);
    alt();
    //////////////destra////////////
    }
}


///////////////////////////////driver/////////////////////////////////

void fwd (int vel1, int vel2, int vel3, int vel4) {
  analogWrite(pwm1,vel1) ;
  analogWrite(pwm2,vel2) ;
  analogWrite(pwm3,vel3) ;
  analogWrite(pwm4,vel4) ;
  digitalWrite(ma1,LOW) ;
  digitalWrite(mb1,HIGH);
  digitalWrite(ma2,LOW) ;
  digitalWrite(mb2,HIGH);
  digitalWrite(ma3,LOW) ;
  digitalWrite(mb3,HIGH);
  digitalWrite(ma4,LOW) ;
  digitalWrite(mb4,HIGH);
  
}
void bk (int vel1, int vel2, int vel3, int vel4) {
  analogWrite(pwm1,vel1) ;
  analogWrite(pwm2,vel2) ;
  analogWrite(pwm3,vel3) ;
  analogWrite(pwm4,vel4) ;
  digitalWrite(mb1,LOW) ;
  digitalWrite(ma1,HIGH);
  digitalWrite(mb2,LOW) ;
  digitalWrite(ma2,HIGH);
  digitalWrite(mb3,LOW) ;
  digitalWrite(ma3,HIGH);
  digitalWrite(mb4,LOW) ;
  digitalWrite(ma4,HIGH);
}
void dx (int vel1, int vel2, int vel3, int vel4) {
  analogWrite(pwm1,vel1) ;
  analogWrite(pwm2,vel2) ;
  analogWrite(pwm3,vel3) ;
  analogWrite(pwm4,vel4) ;
  digitalWrite(ma1,LOW) ;
  digitalWrite(mb1,HIGH);
  digitalWrite(mb2,LOW) ;
  digitalWrite(ma2,HIGH);
  digitalWrite(ma3,LOW) ;
  digitalWrite(mb3,HIGH);
  digitalWrite(mb4,LOW) ;
  digitalWrite(ma4,HIGH);
}
void sx (int vel1, int vel2, int vel3, int vel4) {
  analogWrite(pwm1,vel1) ;
  analogWrite(pwm2,vel2) ;
  analogWrite(pwm3,vel3) ;
  analogWrite(pwm4,vel4) ;
  digitalWrite(mb1,LOW) ;
  digitalWrite(ma1,HIGH);
  digitalWrite(ma2,LOW) ;
  digitalWrite(mb2,HIGH);
  digitalWrite(mb3,LOW) ;
  digitalWrite(ma3,HIGH);
  digitalWrite(ma4,LOW) ;
  digitalWrite(mb4,HIGH);
}
void gdx (int vel1, int vel2, int vel3, int vel4) {
  analogWrite(pwm1,vel1) ;
  analogWrite(pwm2,vel2) ;
  analogWrite(pwm3,vel3) ;
  analogWrite(pwm4,vel4) ;
  digitalWrite(ma1,LOW) ;
  digitalWrite(mb1,HIGH);
  digitalWrite(ma2,LOW) ;
  digitalWrite(mb2,HIGH);
  digitalWrite(mb3,LOW) ;
  digitalWrite(ma3,HIGH);
  digitalWrite(mb4,LOW) ;
  digitalWrite(ma4,HIGH);
}
void gsx (int vel1, int vel2, int vel3, int vel4) {
  analogWrite(pwm1,vel1) ;
  analogWrite(pwm2,vel2) ;
  analogWrite(pwm3,vel3) ;
  analogWrite(pwm4,vel4) ;
  digitalWrite(mb1,LOW) ;
  digitalWrite(ma1,HIGH);
  digitalWrite(mb2,LOW) ;
  digitalWrite(ma2,HIGH);
  digitalWrite(mb3,LOW) ;
  digitalWrite(ma3,HIGH);
  digitalWrite(mb4,LOW) ;
  digitalWrite(ma4,HIGH);
}
void alt() {
  analogWrite(pwm1,0) ;
  analogWrite(pwm2,0) ;
  analogWrite(pwm3,0) ;
  analogWrite(pwm4,0) ;
  digitalWrite(ma1,HIGH);
  digitalWrite(mb1,HIGH);
  digitalWrite(ma2,HIGH);
  digitalWrite(mb2,HIGH);
  digitalWrite(ma3,HIGH);
  digitalWrite(mb3,HIGH);
  digitalWrite(ma4,HIGH);
  digitalWrite(mb4,HIGH);
}


///////////////////////////////encoder/////////////////////////////////

int encoder(){
   aState1 = digitalRead(outputA1); 
   aState2 = digitalRead(outputA2); 
   aState3 = digitalRead(outputA3); 
   aState4 = digitalRead(outputA4);



    if (aState1 != aLastState1){
     if (digitalRead(outputB1) != aState1) {
       counter1 ++;
     } else {
       counter1 --;
     }
   } 
   aLastState1 = aState1;  
   if (aState2 != aLastState2){     
     if (digitalRead(outputB2) != aState2) { 
       counter2 ++;
     } else {
       counter2 --;
     }
   } 
   aLastState2 = aState2;
   if (aState3 != aLastState3){     
    
     if (digitalRead(outputB3) != aState3) { 
       counter3 ++;
     } else {
       counter3 --;
     }
   } 
   aLastState3 = aState3;
   if (aState4 != aLastState4){     
    
     if (digitalRead(outputB4) != aState4) {
       counter4 ++;
     } else {
       counter4 --;
     }
   } 
   aLastState4 = aState4;

   media=abs(counter1)+abs(counter2)+abs(counter3)+abs(counter4);
  media/=4;
  return media;
  }


























///////////////////////////////sensori/////////////////////////////////


void sensori(){
    for(int i = 0; i < 4; i++){ 
   for(int y = 0; y < 2; y++){
   
       pinMode(pingArray[i][y], OUTPUT);
       digitalWrite(pingArray[i][y], LOW);
       delayMicroseconds(2);
       digitalWrite(pingArray[i][y], HIGH);
       delayMicroseconds(5);
       digitalWrite(pingArray[i][y], LOW);

       pinMode(pingArray[i][y], INPUT);
       duration = pulseIn(pingArray[i][y], HIGH);

       cm = microsecondsToCentimeters(duration);
        medie[i][y]=cm;
   }
   
  }


  if(medie[0][0]<8 && medie[0][1]<8){
    raspy[0][0]='1';
    raspy[0][2]='1';
  }else if(medie[1][0]<8 && medie[1][1]<8){
    raspy[0][0]='1';
    raspy[2][0]='1';  
  }else if(medie[2][0]<8 && medie[2][1]<8){
    raspy[2][0]='1';
    raspy[2][2]='1';
  }else if(medie[3][0]<8 && medie[0][1]<8){
    raspy[0][2]='1';
    raspy[2][2]='1';
  }else{
for (int g=0; g<3; g++){
  for (int f=0; f<3; f++){
      raspy[g][f]='0';
    }
  }

  }

  for (int i=0; i<3; i++){
  for (int j=0; j<3; j++){
 
      Serial.print(raspy[i][j]);
    }
    Serial.print("\n");
  }

  
  }

///////////////////////////////////////////////roba rubata//////////////////////////////////////////////////////////////

long microsecondsToCentimeters(long microseconds) {
  return microseconds / 29 / 2;
}

void init_MPU(){
  Wire.begin();
  Wire.beginTransmission(MPU);
  Wire.write(0x6B);  // PWR_MGMT_1 register
  Wire.write(0);     // set to zero (wakes up the MPU-6050)
  Wire.endTransmission(true);
  delay(1000);
}

//Funzione per il calcolo degli angoli Pitch e Roll
double FunctionsPitchRoll(double A, double B, double C){
  double DatoA, DatoB, Value;
  DatoA = A;
  DatoB = (B*B) + (C*C);
  DatoB = sqrt(DatoB);
  
  Value = atan2(DatoA, DatoB);
  Value = Value * 180/3.14;
  
  return (int)Value;
}

//Funzione per l'acquisizione degli assi X,Y,Z del MPU6050
void FunctionsMPU(){
  Wire.beginTransmission(MPU);
  Wire.write(0x3B);  // starting with register 0x3B (ACCEL_XOUT_H)
  Wire.endTransmission(false);
  Wire.requestFrom(MPU,6,true);  // request a total of 14 registers
  AcX=Wire.read()<<8|Wire.read();  // 0x3B (ACCEL_XOUT_H) & 0x3C (ACCEL_XOUT_L)     
  AcY=Wire.read()<<8|Wire.read();  // 0x3D (ACCEL_YOUT_H) & 0x3E (ACCEL_YOUT_L)
  AcZ=Wire.read()<<8|Wire.read();  // 0x3D (ACCEL_YOUT_H) & 0x3E (ACCEL_YOUT_L)
}

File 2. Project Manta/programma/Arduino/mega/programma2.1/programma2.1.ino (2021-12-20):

#include <SPI.h>
#include <Wire.h>
#include <MPU6050_tockn.h>

MPU6050 mpu6050(Wire);

int posx = 0;
int posy = 0;

int campo[10][10][3][3];

#define ma1 6
#define mb1 7
#define pwm1 2

#define ma2 8
#define mb2 9
#define pwm2 3

#define ma3 11
#define mb3 10
#define pwm3 4

#define ma4 13
#define mb4 12
#define pwm4 5

#define velocita 90

bool simulazione = false;
bool msg = true;
byte input = "";

int erroreM = 5; //errore percentuale ancoder
int distanza = 8; //distanza a cui dice che ce un muro
int angolostandard = 90; //angolo
float angoloiniziale = 0;
float k = 0.9; //costante rallentamento



 #define outputA1 22
 #define outputB1 23

 #define outputA2 24
 #define outputB2 25

 #define outputA3 26
 #define outputB3 27

 #define outputA4 28
 #define outputB4 29
 
 int counter1 = 0; 
 int aState1;
 int aLastState1;  

 int counter2 = 0; 
 int aState2;
 int aLastState2; 

 int counter3 = 0; 
 int aState3;
 int aLastState3; 

 int counter4 = 0; 
 int aState4;
 int aLastState4; 

 int media=0;
 bool controllo;
 int pencoder[3];



#define pingPin 32
#define pingPin1 33
#define pingPin2 34
#define pingPin3 35
#define pingPin4 36
#define pingPin5 37
#define pingPin6 38
#define pingPin7 39
#define buttonPin 50
char raspy[3][3];
int pingArray[4][2] = { {pingPin, pingPin7},   //davanti
                        {pingPin1, pingPin2},  //sinistra
                        {pingPin3, pingPin4}, //dietro
                        {pingPin5, pingPin6}  //destra
                      }; 
long duration, cm;
float medie[4][2]; 
float somma;
int errore;
char mystr[2];

int vel = 90;




void setup()
{
if(!simulazione){
  
  Wire.begin();

  pinMode(pwm1,OUTPUT) ;   //we have to set PWM pin as output
  pinMode(ma1,OUTPUT) ;  //Logic pins are also set as output
  pinMode(mb1,OUTPUT) ;

  pinMode(pwm2,OUTPUT) ;   //we have to set PWM pin as output
  pinMode(ma2,OUTPUT) ;  //Logic pins are also set as output
  pinMode(mb2,OUTPUT) ;

  pinMode(pwm3,OUTPUT) ;   //we have to set PWM pin as output
  pinMode(ma3,OUTPUT) ;  //Logic pins are also set as output
  pinMode(mb3,OUTPUT) ;

  pinMode(pwm4,OUTPUT) ;   //we have to set PWM pin as output
  pinMode(ma4,OUTPUT) ;  //Logic pins are also set as output
  pinMode(mb4,OUTPUT) ;

   pinMode (outputA1,INPUT);
   pinMode (outputB1,INPUT);
   pinMode (outputA2,INPUT);
   pinMode (outputB2,INPUT);
   pinMode (outputA3,INPUT);
   pinMode (outputB3,INPUT);
   pinMode (outputA4,INPUT);
   pinMode (outputB4,INPUT);

   mpu6050.begin();
   mpu6050.calcGyroOffsets(true);
   
  Serial.begin(9600);
  Serial1.begin(9600);
  Serial2.begin(9600);
   
   aLastState1 = digitalRead(outputA1);   
   aLastState2 = digitalRead(outputA2);
   aLastState3 = digitalRead(outputA3);
   aLastState4 = digitalRead(outputA4);
  }
  else{
   int n = 0;
    for (int k = 0; k < 10; k++) {
      for (int m = 0; m < 10; m++) {
        for (int i = 0; i < 3; i++) {
          for (int j = 0; j < 3; j++) {
            campo[k][m][i][j] = n;
        
          }
        }
       n++; 
      }
    } 
    Serial.begin(9600);
    Serial1.begin(9600);
    Serial2.begin(9600);
  }
}

void loop()
{
if(!simulazione){
  //Serial1.readBytes(mystr,1);
  //Serial1.println(mystr); 

  //Serial2.readBytes(mystr,1);
  //Serial2.println(mystr); 
  
  if (Serial.available()>0 && msg){
  Serial.println("----- Test movimento motori -----");
  Serial.println("   Utilizzare WASD per muoversi  ");
  Serial.println("  Utilizzare Q ed E per ruotare  ");
  Serial.println(" Utilizzare P per usare i sensori");
  Serial.println("---------------------------------");   
  msg = false;
  }
  if (Serial.available()>0){
    input = Serial.read();
     if (input == 'w')     { avanti(255);       Serial.println("f");}
     else if (input == 'a'){ sinistra(255);     Serial.println("f");}
     else if (input == 's'){ indietro(255);     Serial.println("f");}
     else if (input == 'd'){ destra(255);       Serial.println("f");}
     else if (input == 'q'){ girasinistra(255); Serial.println("f");}
     else if (input == 'e'){ giradestra(255);   Serial.println("f");}
     else if (input == 'p'){ 
      //for (int i=0; i<2; i++){
      sensori();
      delay(100);
      //}
        for (int i=0; i<3; i++){
          for (int j=0; j<3; j++){
            Serial.print(raspy[i][j]);
            }
           Serial.println();
          }
        }
     else if (input == 'f'){ ferma();}
    }
  }

/////////////////simulazione////////////////////
  
  else{ 
    if (Serial.available()>0 && msg){
  Serial.println("----- Test movimento simulazione -----");
  Serial.println("      Utilizzare WASD per muoversi    ");
  Serial.println("   Utilizzare P per usare i sensori   ");
  Serial.println("--------------------------------------");  
  msg = false;
  }
  if (Serial.available()>0){
    input = Serial.read();
     if (input == 'w')     { if(posy>0){posy--;} delay(2000); Serial.println("f"); }
     else if (input == 'a'){ if(posx>0){posx--;} delay(2000); Serial.println("f"); }
     else if (input == 's'){ if(posy<9){posy++;} delay(2000); Serial.println("f"); }
     else if (input == 'd'){ if(posx<9){posx++;} delay(2000); Serial.println("f"); }
     else if (input == 'p'){ printsim(); }
    }

  }
}


///////////////////////////////print sim///////////////////////

void printsim(){
  Serial.println("S");
  for (int i = 0; i < 3; i++) {
          for (int j = 0; j < 3; j++) {
            Serial.print(campo[posx][posy][i][j]);       
          }
          Serial.println();
        }
  Serial.println("S");
}


////////////////////////driver/////////////////////////////

void motori(int velocita1, int velocita2, int velocita3, int velocita4, int driverMB1, int driverMA1, int driverMB2, int driverMA2, int driverMB3, int driverMA3, int driverMB4, int driverMA4) {
  analogWrite(pwm1,velocita1);
  analogWrite(pwm2,velocita2);
  analogWrite(pwm3,velocita3);
  analogWrite(pwm4,velocita4);
  digitalWrite(mb1,driverMB1);
  digitalWrite(ma1,driverMA1);
  digitalWrite(mb2,driverMB2);
  digitalWrite(ma2,driverMA2);
  digitalWrite(mb3,driverMB3);
  digitalWrite(ma3,driverMA3);
  digitalWrite(mb4,driverMB4);
  digitalWrite(ma4,driverMA4);

  
}

///////////////////////////////motori/////////////////////////////////

void avanti (int vel) { //direzioni dei motori 
  movimento('w');
}
void indietro (int vel) {
  movimento('s');
}
void destra (int vel) {
  movimento('d');
}
void sinistra (int vel) {
  movimento('a');
}
void giradestra (int vel) {
  movimento('e');
}
void girasinistra (int vel) {
  movimento('q');
}
void ferma () {
  motori(0, 0, 0, 0, HIGH, HIGH, HIGH, HIGH, HIGH, HIGH, HIGH, HIGH);
}

///////////////////////////////encoder/////////////////////////////////

int encoder(){
   aState1 = digitalRead(outputA1); 
   aState2 = digitalRead(outputA2); 
   aState3 = digitalRead(outputA3); 
   aState4 = digitalRead(outputA4);
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

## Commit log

2021-12-20 Version 1
    [Back x1.dxf, Back.dxf, Bottom x1.dxf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]
2022-02-17 i cazzi miei
    [Cubo v8.f3d, Cubo v8.stl, cagacubi v8.f3d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]
2022-03-12 mannaggia il putin
    [Back x1.dxf, Back.dxf, Bottom x1.dxf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]
2022-03-12 put in gerber
2022-03-27 spostato roba
    [Back x1.dxf, Back.dxf, Bottom x1.dxf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]
2022-04-07 Create cagacubi v9.stl
    [cagacubi v9.stl]
2022-04-22 Create Premio Gara.stl
    [Premio Gara.stl]
2022-05-05 finito tutto a parte la pinza
2022-05-11 Create Premio v2.stl

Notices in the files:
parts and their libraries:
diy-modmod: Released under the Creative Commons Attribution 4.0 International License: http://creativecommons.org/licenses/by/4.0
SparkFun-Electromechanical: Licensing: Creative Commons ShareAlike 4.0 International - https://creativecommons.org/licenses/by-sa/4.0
